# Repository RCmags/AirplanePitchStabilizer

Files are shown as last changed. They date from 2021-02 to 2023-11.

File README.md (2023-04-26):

# Pitch-axis stabilizer for a tail-less airplane :airplane:
This arduino sketch is a servo controller that stabilizes the pitch-axis of a radio-controlled airplane. It's intended to be used on tail-less aircraft to enhance their otherwise marginal stability. Nonetheless, the controller can work on machines with sufficient passive stability. It can increase the effective __static margin__ and allow the center of mass to be shifted aft. This tends to increase the lift-to-drag ratio of the aircraft.  

## State measurement
Pitch stabilization can be accomplished in a variety of ways. These include directly measuring the relative airflow across the aircraft, or measuring changes in the motion and inferring the state of the airflow. 

__Angle of attack sensor__:
The attitude of an airplane is mainly determined by the aerodynamic forces acting upon it. For the pitch axis, the torque generated by these forces is primarily a function of the [angle of attack](https://en.wikipedia.org/wiki/Angle_of_attack). By measuring this angle, one can apply corrective actions that rotate the aircraft towards a particular orientation. Therefore, we can gauge the stability of the aircraft based on how quickly it converges towards said angle, or conversely, its instability if it diverges.    

The simplest angle-of-attack sensor is a [low-friction potentiometer attached to a weathervane](https://www.ilmailu.org/forum/index.php?action=dlattach;topic=5147.0;attach=10336). 

<p align="center"> 
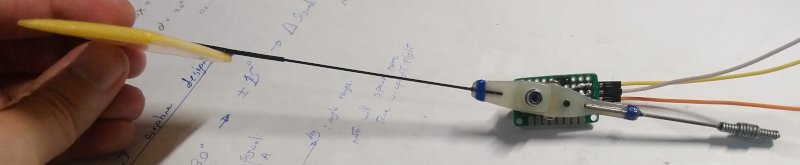
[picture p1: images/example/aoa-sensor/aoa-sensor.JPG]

</p>

As the weathervane will closely follow the local airflow, the deflection of the weathervane is proportional to the angle of attack.

__Inertial measurement unit (IMU)__: 
One can maintain the attitude of the aircraft by measuring its change in orientation and providing an appropriate correction. In this case, we use the angular velocity from a gyroscope as the proportional term in a PID controller. The integral term becomes the angular deflection and is approximately equal to the angle of attack for small external disturbances. As such, we can approximate the behaviour obtained with an angle of attack sensor without having to use a weathervane.  

## Control mechanisms
No matter how the aircraft's state is measured, it is still necessary to use a mechanism to physically rotate the vehicle. The code considers the following designs:

__Trailing edge flaps__: This is the most common way to control a tail-less airplane. It involves deflecting a hinged section of the aft portion of the wing. 

<p align="center"> 
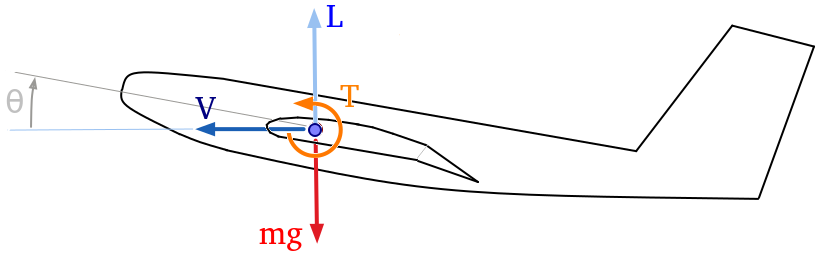
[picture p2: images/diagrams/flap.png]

</p>

The torque generated by these deflections depends on the airspeed and the chord of the wing. If the wing is wider, the flaps are further aft relative to the center of mass and generate a larger torque. Conversely, a higher airspeed causes the changes in lift for a given flap deflection to increase, and this increases the torque. 

Despite their simplicity, trailing edge flaps become _increasingly ineffective_ if the wing has a large [aspect ratio](https://en.wikipedia.org/wiki/Aspect_ratio_(aeronautics)) (small chord) or if the aircraft flies slowly. This configuration is best suited for high speed flight with stubby wings.

__Weight shift__: It is also possible to control the pitch axis by moving the lift vector relative to the center of mass. This comes from the very definition of torque: 

$$ T = d \times F $$

Rather than changing the force __F__ at a known distance __d__ (as with trailing edge flaps), we change the distance in accord to a known force. 

<p align="center"> 
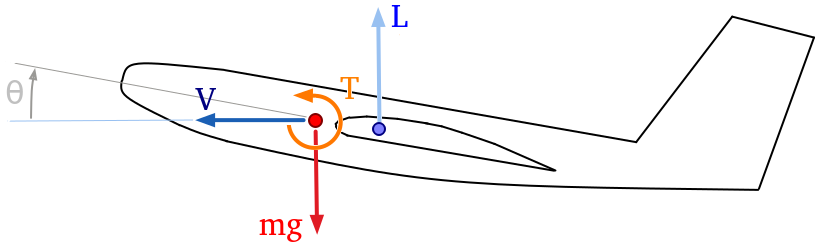
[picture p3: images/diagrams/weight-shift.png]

</p>

In level flight, the net force upon the aircraft is mainly lift, and it must necessarily counter weight. Hence, changing the distance shifts the weight.

$$ F = L = mg $$
 
The effectiveness of this control mechanism is proportional to the magnitude of the lift vector. If the lift is large, small deflections are required. However, the deflections become very large as the lift becomes small. This relationship breaks down with zero lift as there is no force to generate a torque. Despite this flaw, weight shift is a valid control mechanism so long as the airplane's wing remains _loaded_. 

Unlike trailing edge flaps, weight shift does _not_ lose effectiveness at low speed. As long as the aircraft is not accelerating downwards, the control effectiveness will remain the same.  
  
## Schematics
Since there are a few variants of the controller depending on the stabilization method, there are different schematics as well. 

__Nano:__ There are two versions of the sketch for the arduino nano. Despite this, it should be compatible with similar boards. Each version uses the stabilization concepts discussed above. 

- Angle of attack sensor: This schematic assumes a potentiometer is used as the sensor, but any analog sensor will work. A hall sensor is a low-friction alternative of the potentiometer.

<p align="center"> 
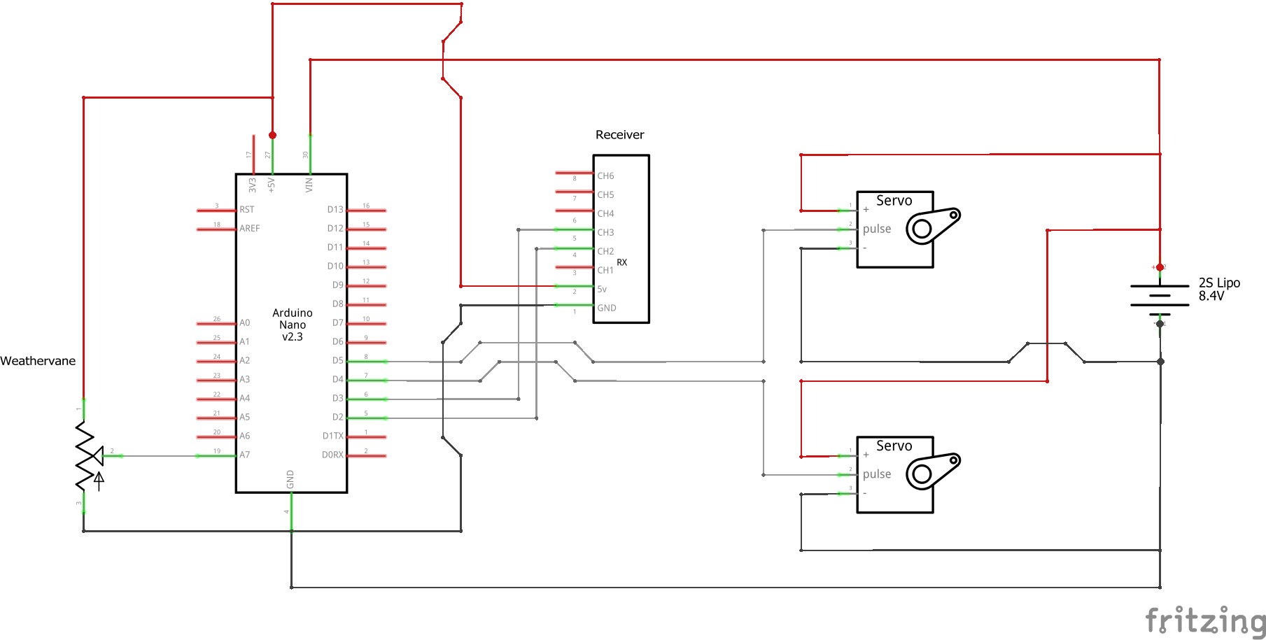
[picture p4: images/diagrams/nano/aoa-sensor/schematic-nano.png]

</p>

- IMU sensor: The code is designed around an [MPU-6050 IMU](https://invensense.tdk.com/products/motion-tracking/6-axis/mpu-6050/) but the general structure will work for any IMU.

<p align="center"> 
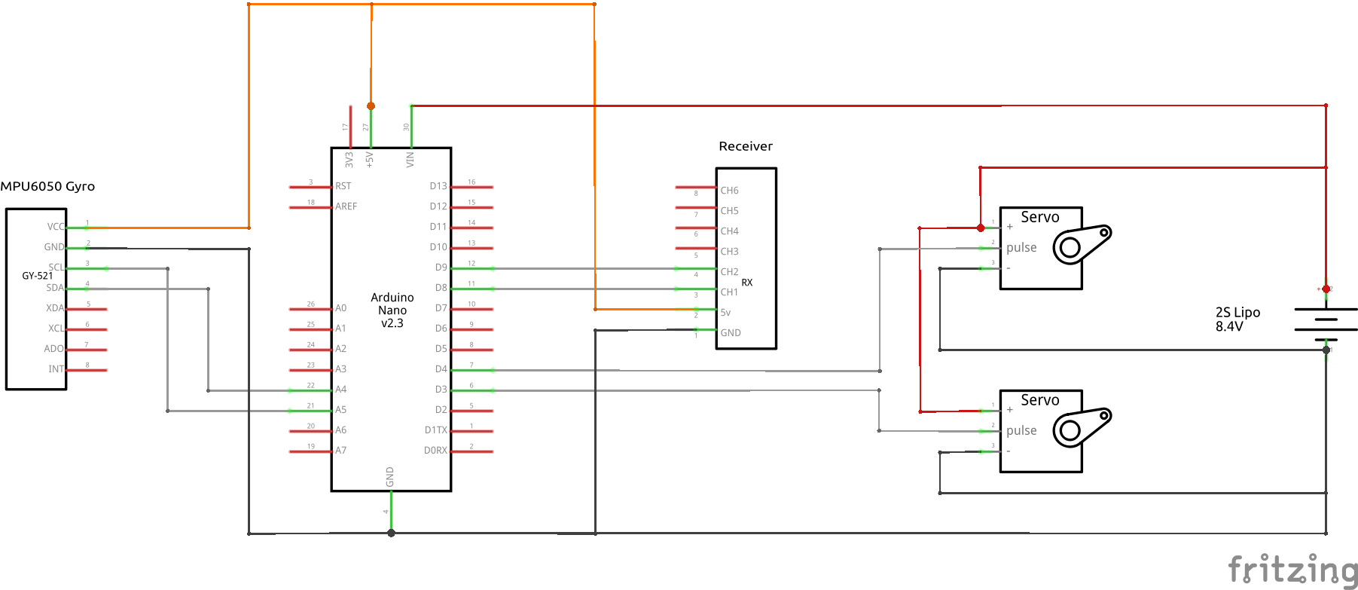
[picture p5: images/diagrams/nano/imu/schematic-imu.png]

</p>

__DigiSpark ATTiny85__: The version of the sketch does not have the option for an IMU. Rather, it serves as a lighter alternative to the nano when using an angle of attack sensor.

<p align="center"> 
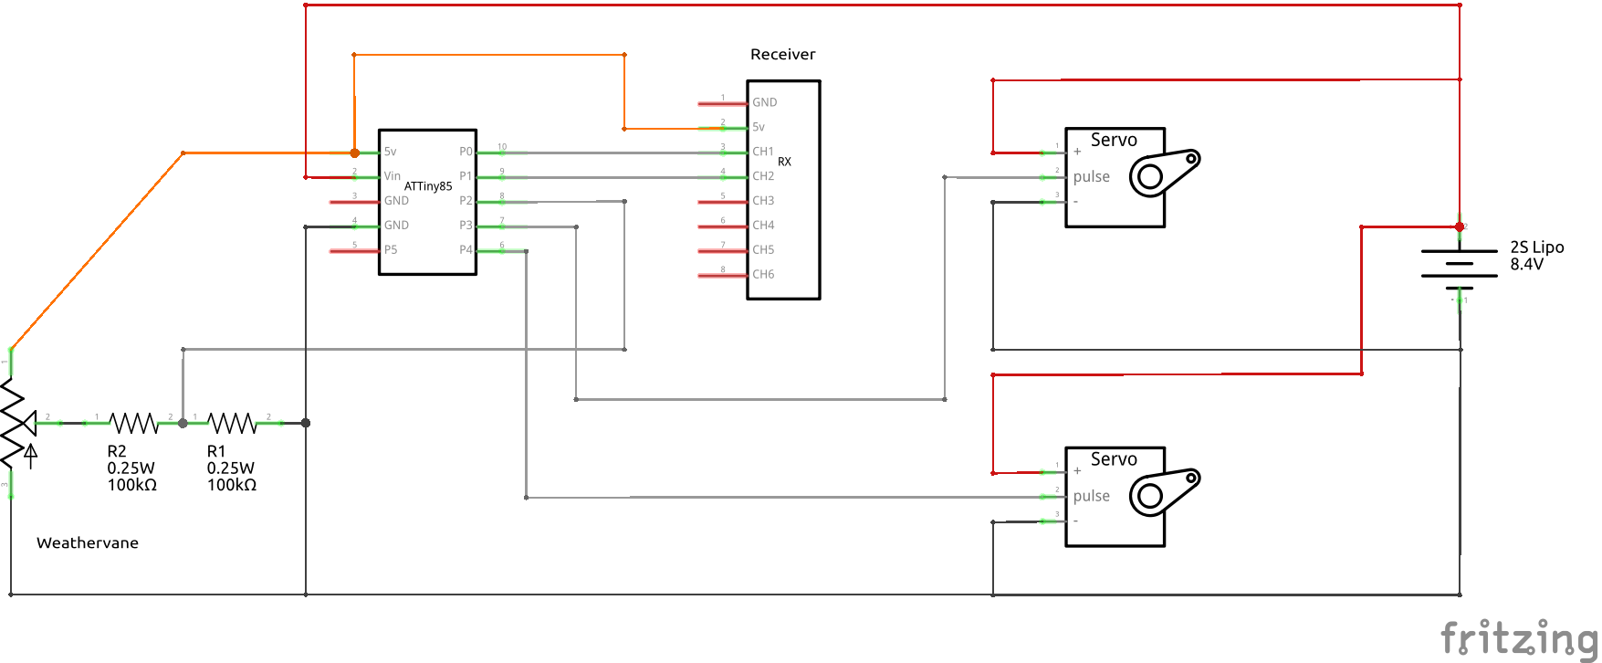
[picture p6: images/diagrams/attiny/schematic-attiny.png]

</p>

## Dependencies
The IMU version of the code requires the following libraries:

- [basicMPU6050](https://github.com/RCmags/basicMPU6050)
- [imuFilter](https://github.com/RCmags/imuFilter)

The ATTiny code requires [ATTinyCore](https://github.com/SpenceKonde/ATTinyCore) to compile. 

## References
See these pages for previous projects that inspired this work:

- [Active flying wing pitch stabilizer concept](http://www.charlesriverrc.org/articles/asfwpp/lelke_activepitch.htm)
- [Unstable Tailless Demonstrator - video](https://www.youtube.com/watch?v=JfKrUbJYk74)

## Examples

- Airplane with a slightly aft center of mass that is controlled by trailing edge flaps: 

<p align="center">
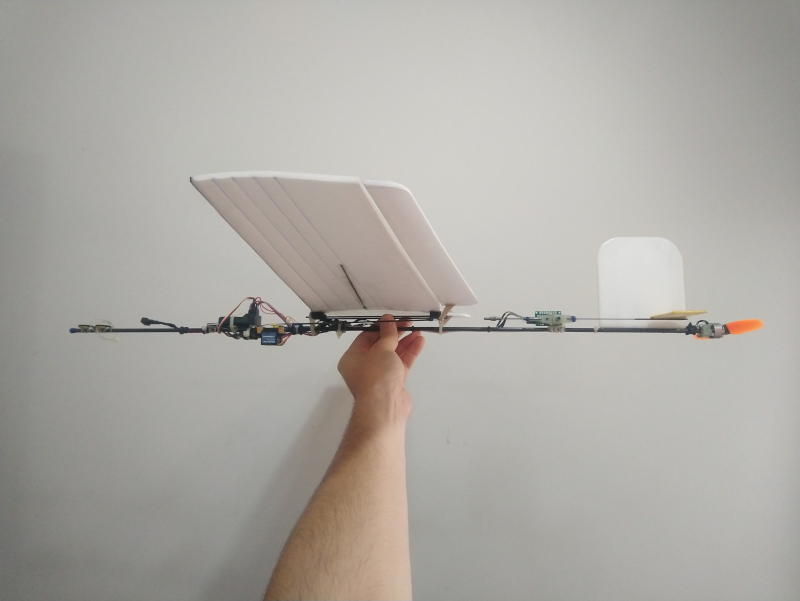
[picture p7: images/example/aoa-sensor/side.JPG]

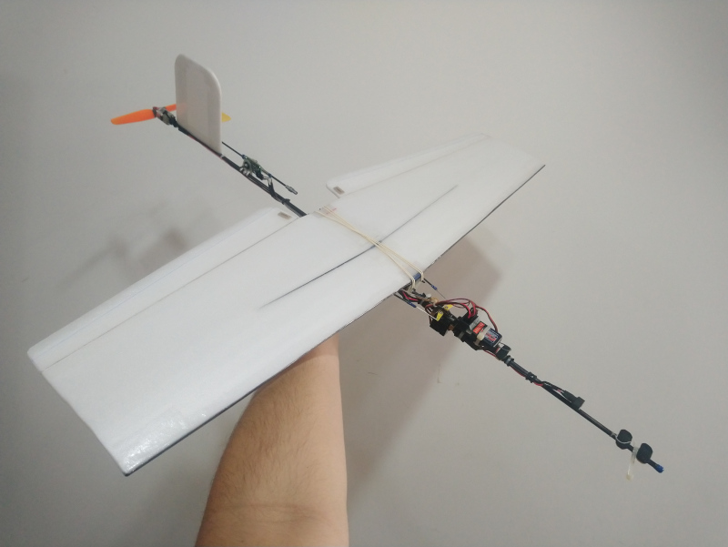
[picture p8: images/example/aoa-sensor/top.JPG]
 
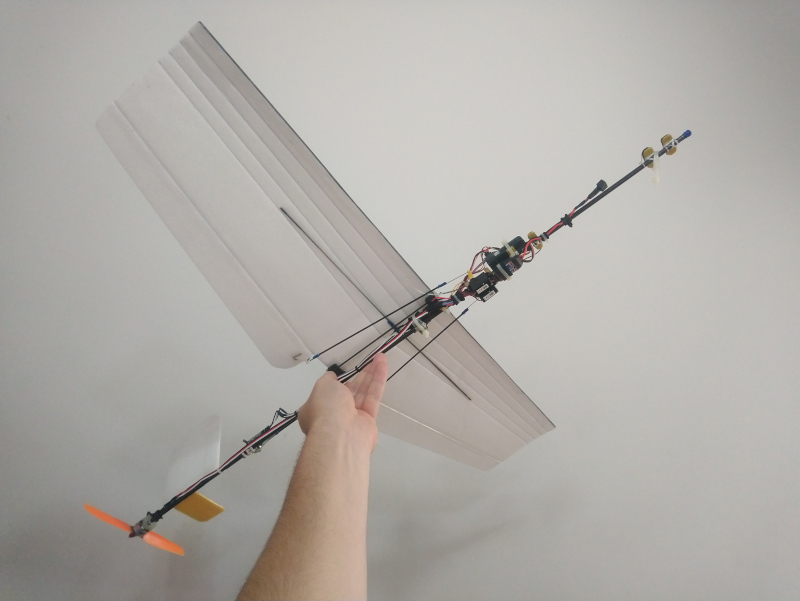
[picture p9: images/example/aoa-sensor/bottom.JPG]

</p>

- Airplane that is stabilized and controlled by weight shift: 

<p align="center">
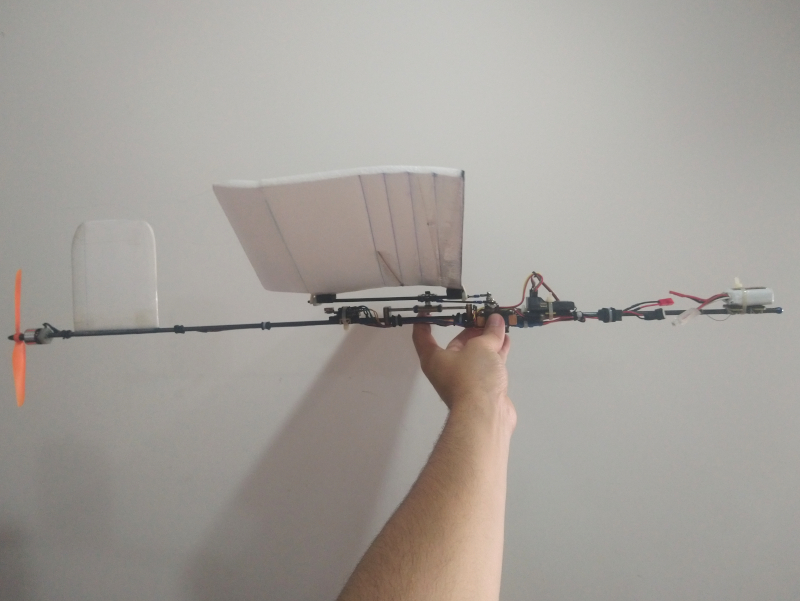
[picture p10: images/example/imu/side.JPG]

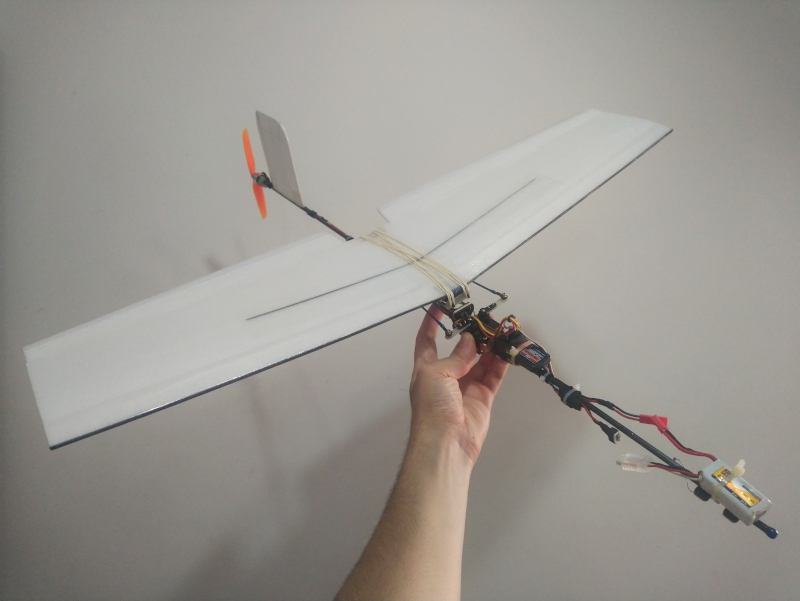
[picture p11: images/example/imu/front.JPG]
 
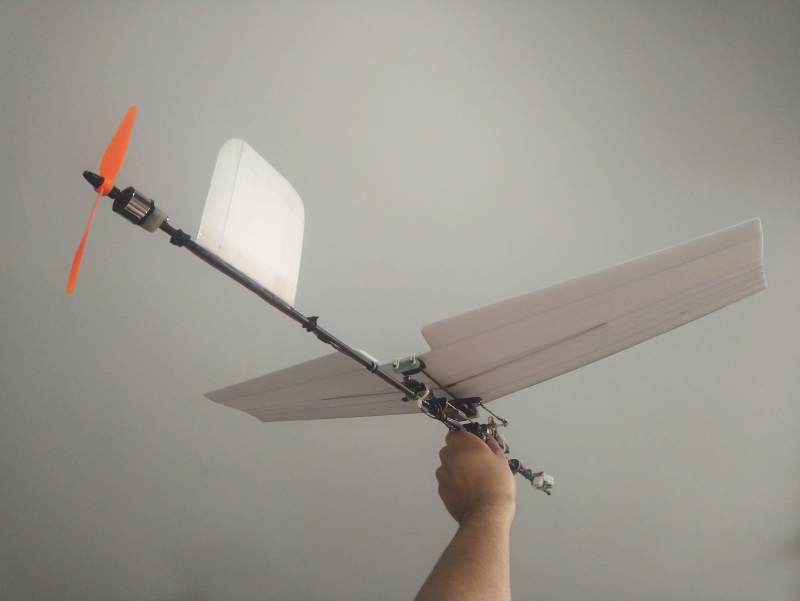
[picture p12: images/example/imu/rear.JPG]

</p>

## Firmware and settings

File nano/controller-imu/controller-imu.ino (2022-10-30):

/* FLYING WING CONTROLLER */

/* Arduino NANO sketch to stabilize an RC flying wing controlled by weight-shift or trailing edge flaps. 
 * It commands two servos and applies V-tail mixing to stabilize the pitch axis.
 * Author: RCmags https://github.com/RCmags
 * 
 * NOTE: 
 * This sketch uses an MPU6050 IMU (gyroscope and accelerometer) to stabilize pitch. It assumes that only 
 * lift and gravity act on the aircraft, and that any external torques are negligible. For stability at 
 * all airspeeds, the wing should have close to no pitching moment.
*/

//=============== Connections ================
// See included schematic
  // Inputs:
// Pin 8  -> Receiver CH1
// Pin 9  -> Receiver CH2
// Pin A5 -> Sensor SCL
// Pin A4 -> Sensor SDA
  // Outputs:
// Pin 2  -> Left  wing servo
// Pin 3  -> Right wing servo 

//=================== Code ===================
#include <Servo.h>
#include "parameters.h"
#include "imu.h"
#include "fusion.h"

//----- constants
constexpr int PWM_MID_L = PWM_MID + TRIM_LEFT;
constexpr int PWM_MID_R = PWM_MID - TRIM_RIGHT;

constexpr float ANGVEL_SCALE = GRAVITY / VELOCITY;   
constexpr float ANGVEL_MIN = (ACCEL_MIN - 1) * ANGVEL_SCALE;
constexpr float ANGVEL_MAX = (ACCEL_MAX - 1) * ANGVEL_SCALE; 

//----- global variables 
Servo servo[2]; 
volatile uint16_t pwm_input[2] = {0};

//----- Input signals
// PORTB = {8 .. 13} -> using pins {8 .. 9} = B00000011

/* port change interrupt to read PWM inputs from receiver */
ISR( PCINT0_vect ) {
  static uint32_t initial_time[2] = {0}; 
  static uint8_t port_last = PINB;  
  
  // port changes
  uint32_t current_time = micros(); 
  uint8_t port_rise = ~port_last & PINB;
  uint8_t port_fall = port_last & ~PINB;
  
  // find changing pins
  for( uint8_t index = 0; index < 2; index += 1) {
    uint8_t mask = B00000001 << index;  // Start at PCINT0
    if( port_rise & mask ) {                
        initial_time[index] = current_time;
    } else if ( port_fall & mask ) {       
        pwm_input[index] = current_time - initial_time[index];
    }
  }
  port_last = PINB;    
}

void setupISR() {
  // enable PORTB interrupts  
  PCICR |= (1 << PCIE0);
  // enable PCINT for pins 8-9     
  PCMSK0 |= (1 << PCINT0);   
  PCMSK0 |= (1 << PCINT1);
  // set as input
  pinMode(8, INPUT_PULLUP);   
  pinMode(9, INPUT_PULLUP); 
}

//----- Input filter

/* average of rx signals */
int* calibrateInputs() {  
  uint32_t sum[2] = {0};
  for( uint8_t count = 0; count < NUMBER_MEAN; count += 1 ) {
    sum[0] += pwm_input[0];
    sum[1] += pwm_input[1];
    delay(20);                  // period of 50hz pwm signal
  }
  static int output[2];         // store value to limit scope
  output[0] = sum[0] / NUMBER_MEAN;
  output[1] = sum[1] / NUMBER_MEAN;
  return output; 
}

/* make variable zero within bounds */
float deadband(float input, const float MIN, const float MAX) {
  return input > MAX ? input - MAX :
         input < MIN ? input - MIN : 0;  
}

/* remove noise from PWM inputs then scale and center */
void filterInputs(float* output) {
  static int* pwm_mean = calibrateInputs();
  static int filter[2] = {0};  
  
  for( uint8_t index = 0; index < 2; index += 1 ) {
    // remove noise
    int input = int( pwm_input[index] );
    int change = input - filter[index]; 
    filter[index] += deadband(change, -INPUT_CHANGE, INPUT_CHANGE);

    // center output
    output[index] = filter[index] - pwm_mean[index];
    output[index] = deadband( output[index], -INPUT_DEADBAND, INPUT_DEADBAND);
  }
  // scale output
  output[0] *= float(GAIN_ROLL);    // roll
  output[1] *= float(GAIN_PITCH);   // pitch
}

//----- PID controller

#ifdef USING_WEIGHT_SHIFT

/* gain to maintain constant torque indifferent of wing load */
float gainLift(float accel) {
  return accel == 0 ? 0 : 1/accel;
}
#endif

/* time integral of variable */
float integral(float input) {
  static uint32_t last_time = micros();
  static float value[2] = {0};

  // update timer
  uint32_t curr_time = micros();
  float dt = float(curr_time - last_time)*1e-6;
  last_time = curr_time;

  // trapezoidal rule
  constexpr float MAX = DEG_TO_RAD * ANGLE_MAX;

  value[0] += 0.5*( input + value[1] )*dt;
  value[1] = input;

  // prevent windup
  value[0] = constrain(value[0], -MAX, MAX);
  return value[0];
}

/* limit wing loading */
float restrictRate(float input, float accel) {  
  // limit target angular velocity
  constexpr float SCALE = (150 * DEG_TO_RAD) / 500.0;     // Convert 500 ms to 150 deg/s
  input *= SCALE;
  input = constrain(input, ANGVEL_MIN, ANGVEL_MAX); 

  // correct rate at acceleration limits
  accel = deadband(accel, ACCEL_MIN, ACCEL_MAX);
  return input - float(GAIN_ACCEL)*accel;
}

/* PID controller to stabilize pitch axis */
float PIDcontroller(float input) {  
  // state 
  float accel = imu.az();       // acceleration due to lift
  #ifdef NEGATE_ACCEL
    accel = -accel;
  #endif

  float angvel_m = imu.gx();    // pitch-axis rotation
  #ifdef NEGATE_GYRO
    angvel_m = -angvel_m;
  #endif
 
  // controller  
  float angvel_t = restrictRate(input, accel);
  float angvel = angvel_m - angvel_t;     
  float angle = integral(angvel);
    // use P and I terms
  float output = float(GAIN_INT)*angle + float(GAIN_PROP)*angvel;

  #ifdef USING_WEIGHT_SHIFT
    return output * gainLift(accel); 
  #else
    return output;
  #endif
}

/* bias controls to self upright */
void autoLevel(float* input) { 
    // horizontal angles
    vec3_t zvec = fusion.getZaxis(LOCAL_FRAME);
    float angle_y = atan2(zvec.x, zvec.z);
    float angle_x = atan2(zvec.y, zvec.z); 
    
    // control rates
    constexpr float ANGLE = ANGLE_TRIM * DEG_TO_RAD;
    input[1] += float(GAIN_ANG_PITCH) * (angle_x - ANGLE);   // pitch
    input[0] += float(GAIN_ANG_ROLL) * angle_y;              // roll
}

//----- Servos
void setupServos() {    
  pinMode(PIN_SERVO_LEFT, OUTPUT);
  pinMode(PIN_SERVO_RIGHT, OUTPUT);
  servo[0].attach(PIN_SERVO_LEFT);
  servo[1].attach(PIN_SERVO_RIGHT);
  // default position
  servo[0].writeMicroseconds(PWM_MID_L);
  servo[1].writeMicroseconds(PWM_MID_R);
}

//----- Main loop

void setup() {
  setupISR();
  setupServos();
  
  #ifndef USING_MANUAL_CONTROL 
    imu.setup();  // use sensor 
    imu.setBias();
    setupFusion();
  #endif
}

void loop() {
  // update gyro calibration 
  imu.updateBias();
  updateFusion();

  // combine inputs
  float input[2]; filterInputs(input);

  #ifndef USING_MANUAL_CONTROL
    #ifdef USING_AUTO_LEVEL
      autoLevel(input);   
    #endif
    input[1] = PIDcontroller( -input[1] );
  #endif
  
  float mix1 = input[0] + input[1];
  float mix2 = input[0] - input[1];
  
  // command servos  
  mix1 = constrain(mix1, -PWM_CHANGE, PWM_CHANGE );
  mix2 = constrain(mix2, -PWM_CHANGE, PWM_CHANGE );

  servo[0].writeMicroseconds( PWM_MID_L + mix1 );    // left wing   
  servo[1].writeMicroseconds( PWM_MID_R + mix2 );    // right wing
}

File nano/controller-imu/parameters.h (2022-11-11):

/*      CONSTANT     |    VALUE   |  UNIT  |   DESCRIPTION */
/*=========================================================*/
//                  1. Control inputs 
//----------------------------------------------------------
#define GAIN_PITCH        1.0                 // Change in target angle of attack due pitch commands. 
#define GAIN_ROLL        -0.9                 // Asymmetric sweep, CH1

//----------------------------------------------------------
//                  2. Servo trims
//----------------------------------------------------------
#define TRIM_LEFT         120      // us       // left  wing 
#define TRIM_RIGHT        0        // us       // right wing

//----------------------------------------------------------
//                  3. Output PWM signal
//----------------------------------------------------------
#define PWM_MID           1500    // us       // Center/middle servo position
#define PWM_CHANGE        750     // us       // Maximum change in servo position

//----------------------------------------------------------
//                  4. Pitch Stabilization
//----------------------------------------------------------
  // I. PID Controller [negate to reverse]                       
#define GAIN_INT          1200.0              // Integral gain. Adjusts spring response
#define GAIN_PROP         1100.0               // Proportional gain. Adjusts damping response
#define ANGLE_MAX         30      // deg      // Angle at which integral term saturates
  
  // II. Self levelling
#define GAIN_ANG_ROLL     200                 // Gain to set roll input to self-level aircraft
#define GAIN_ANG_PITCH   -180                 // Gain to set pitch rate to self-level aircraft 
#define ANGLE_TRIM       -8.0     // deg      // target flight angle relative to horizon
  
  // III. Maximum control rates                          
#define ACCEL_MIN         0.1     // g-force  // Minimum allowable wing load. Seen at max down elevator
#define ACCEL_MAX         3.0     // g-force  // Maximum allowable wing load. Seen at max up elevator
                                              /* NOTE: ACCEL_MIN < ACCEL_MAX */
#define VELOCITY          9.0     // m/s      // Average airspeed. A larger speed reduces the pitch rate 
#define GAIN_ACCEL        0.0                 // Load correction gain. Restricts maximum and minimum accelerations 
                                              /* GAIN_ACC must be positive */

//----------------------------------------------------------
//                  5. Input signal filter
//----------------------------------------------------------
#define INPUT_DEADBAND    24      // us       // deadband near center-stick to prevent integrator drift.
#define INPUT_CHANGE      18      // us       // Change in PWM signal needed to update receiver inputs

//----------------------------------------------------------
//                  6. Settings
//---------------------------------------------------------- 
#define NEGATE_ACCEL                          // Uncomment if sensor reads -1.0g when aircraft is upright (reversed z-axis). 
#define NEGATE_GYRO                           // Uncomment if pitch correction is backwards
#define USING_AUTO_LEVEL                      // Uncomment to enable self-leveling correction
#define USING_WEIGHT_SHIFT                    // Uncomment for weight-shift pitch control.  
                                              /* Enables gain that modifies pitch corrections with angle of attack */
//#define USING_MANUAL_CONTROL                  // Uncomment to dissable pitch stabilization and enable manual input

//----------------------------------------------------------
//                  7. Miscellaneous 
//---------------------------------------------------------- 
#define PIN_SERVO_LEFT    2
#define PIN_SERVO_RIGHT   3
#define NUMBER_MEAN       50                  // number of readings used for input calibration
#define GRAVITY           9.81    // m/^2     // acceleration due to gravity [m/s^2]

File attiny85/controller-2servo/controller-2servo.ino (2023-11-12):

/* FLYING WING CONTROLLER */

/* ATTiny85 sketch to stabilize an RC flying wing controlled by weight-shift or trailing edge flaps. 
 * It commands two servos and applies V-tail mixing to stabilize the pitch axis.
 * Author: RCmags https://github.com/RCmags
 * 
 * NOTE: Code is intended to be used with ATTinyCore
*/

//=============== Connections ================
// See included schematic
  // Inputs:
// Pin 0 -> Receiver CH1
// Pin 1 -> Receiver CH2
// Pin 2 -> middle of voltage divider 
  // Outputs:
// Pin 3 -> Left  wing servo
// Pin 4 -> Right wing servo 

/* VOLTAGE DIVIDER is required for analog input */
/* GND --/\/\/\-- MIDDLE --/\/\/\-- SENSOR_OUT  */
/*        100K              100K                */

//=================== Code ===================
#include <Servo_ATTinyCore.h>
#include "parameters.cpp"

//----- constants
constexpr int PWM_MID_L = PWM_MID + TRIM_LEFT;
constexpr int PWM_MID_R = PWM_MID - TRIM_RIGHT*GAIN_CORRECTION;

//---- global variables 
Servo servo[2]; 
volatile uint16_t pwm_input[2] = {0};

//----- Input signals
// PORTB = {0 .. 5} -> using pins {0 .. 1} = B00000011

/* port change interrupt to read PWM inputs from receiver */
ISR( PCINT0_vect ) {
  static uint32_t initial_time[2] = {0}; 
  static uint8_t port_last = PINB;  
  
  // port changes
  uint32_t current_time = micros(); 
  uint8_t port_rise = ~port_last & PINB;
  uint8_t port_fall = port_last & ~PINB;
  
  // find changing pins
  for( uint8_t index = 0; index < 2; index += 1) {
    uint8_t mask = B00000001 << index;  // Start at PCINT0
    if( port_rise & mask ) {                
        initial_time[index] = current_time;
    } else if ( port_fall & mask ) {       
        pwm_input[index] = current_time - initial_time[index];
    }
  }
  port_last = PINB;    
}

void setupISR() {
  // enable pin change interrupts
  GIMSK |= (1 << PCIE);     
  // set pins as PCINT
  PCMSK |= (1 << PCINT0);   
  PCMSK |= (1 << PCINT1);
  // set as input
  pinMode(PB0, INPUT_PULLUP);   
  pinMode(PB1, INPUT_PULLUP); ; 
}

//----- Input filter

/* remove noise from PWM inputs then scale and center */
void filterInputs(float* output) {
  static int filter[2] = {0};  
  
  // apply deadband filter
  for( uint8_t index = 0; index < 2; index += 1 ) {
    int change = int( pwm_input[index] ) - filter[index]; 
    filter[index] = change >  INPUT_CHANGE ? int(pwm_input[index]) - INPUT_CHANGE :
                    change < -INPUT_CHANGE ? int(pwm_input[index]) + INPUT_CHANGE : filter[index];
  }
  // scale and center inputs
  output[0] = float( filter[0] - PWM_MID )*GAIN_ROLL;    // roll
  output[1] = float( filter[1] - PWM_MID )*GAIN_PITCH;   // pitch
}

//----- Analog sensor

/* read sensor and calibrate to degrees */
float readSensor() {
  constexpr float SLOPE = float(ANGLE_MAX - ANGLE_MIN) / float(ANALOG_MAX - ANALOG_MIN);
  constexpr int   CONST = (ANALOG_MAX + ANALOG_MIN)/2 + ANALOG_OFFSET;
  // scale reading
  int value = analogRead(1) - CONST;      // PB2 -> ADC1 
  return SLOPE*float(value);
}

/* remove noise from analog sensor and calculate derivative */
void filterSensor(float *xbar, float *dxdt) {
  // store state
  static uint32_t last_time = micros();
  static float x[2] = {0}, v = 0;

  // time change
  uint32_t curr_time = micros();
  float dt  = float(curr_time - last_time)*1e-6;
  last_time = curr_time; 

  // alpha-beta filter:
  constexpr float BETA = ALPHA * ALPHA * 0.25;
    // error
  float xi = readSensor();
  float dx = 0.5*( xi - x[1] );
    // position
  float xnew = x[0];
  xnew += v*dt;  
  xnew += ALPHA * dx; 
    // velocity
  v += BETA * dx/dt;

  // store past position
  x[1] = x[0];
  x[0] = xnew;

  // return smoothed value and derivative
  *xbar = xnew;
  *dxdt = v;
}

//----- PID controller

#ifdef USING_WEIGHT_SHIFT

/* gain to maintain constant torque indifferent of angle of attack */
float gainAngle(float angle) {
  return angle == 0 ? 0 : AOA_TRIM/angle;
}
#endif

/* PID controller to stabilize pitch axis */
float PIDcontroller(float input) {
  float angle; float angle_deriv; filterSensor(&angle, &angle_deriv);
  
  // desired angle of attack
  constexpr float SCALE = 10.0 / 500.0;     // Convert 500 ms to 10 degrees
  
  float targ_angle = SCALE*input + AOA_TRIM;
  targ_angle = constrain(targ_angle, AOA_MIN, AOA_MAX);
  
  // use P and D terms
  float output = GAIN_PROP*(angle - targ_angle) + GAIN_DERIV*angle_deriv;
  
  #ifdef USING_WEIGHT_SHIFT
    return output * gainAngle(angle); 
  #else
    return output;
  #endif
}

//----- Servos

void setupServos() {    
  pinMode(PB3, OUTPUT);
  pinMode(PB4, OUTPUT);
  servo[0].attach(PB3);
  servo[1].attach(PB4);
  // default position
  servo[0].writeMicroseconds(PWM_MID_L);
  servo[1].writeMicroseconds(PWM_MID_R);
}

//----- Main loop

void setup() {
  setupISR();
  setupServos();
  pinMode(PB2, INPUT_PULLUP); // sensor
}

void loop() {
  // combine inputs
  float input[2]; filterInputs(input);

  #ifdef USING_MANUAL_CONTROL
    float output = input[1];                    // directly use rx input
  #else
    float output = PIDcontroller( -input[1] );  // pitch input controls target AoA
  #endif

  // limit
  output = constrain(output, -PWM_CHANGE_PITCH, PWM_CHANGE_PITCH); 

  // mix
  float mix1 = input[0] + output; 
  float mix2 = input[0] - output;
  
  // command servo  
  mix1 = constrain(mix1, -PWM_CHANGE, PWM_CHANGE);
  mix2 = constrain(mix2, -PWM_CHANGE, PWM_CHANGE) * GAIN_CORRECTION;

  servo[0].writeMicroseconds( PWM_MID_L + mix1 );    // left wing
  servo[1].writeMicroseconds( PWM_MID_R + mix2 );    // right wing 
}

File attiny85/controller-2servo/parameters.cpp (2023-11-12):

/*      CONSTANT     |    VALUE   |  UNIT  |   DESCRIPTION */
/*=========================================================*/
//                  1. Control inputs
//----------------------------------------------------------
#define GAIN_PITCH       -1.0               // Change in target angle of attack due pitch commands 
#define GAIN_ROLL         0.65               // Asymmetric sweep/ailerons

//----------------------------------------------------------
//                  2. Servo trims
//----------------------------------------------------------
#define TRIM_LEFT         0       // us     // left  wing 
#define TRIM_RIGHT        0       // us     // right wing
                                            /* Adjust so the aircraft maintains altitude without rolling or pitching */

//----------------------------------------------------------
//                  3. Output PWM signal
//----------------------------------------------------------
#define PWM_MID           1500    // us     // Center/middle servo position
#define PWM_CHANGE        800     // us     // Maximum change in servo position relative to middle
#define PWM_CHANGE_PITCH  800     // us     // Maximum change in servo position for pitch 
#define GAIN_CORRECTION   0.6               // Correction factor to make servos move symmetrically

//----------------------------------------------------------
//                  4. Signal filters
//----------------------------------------------------------
#define INPUT_CHANGE      12      // us     // Change in PWM signal needed to update receiver inputs
#define ALPHA             0.15              /* Gain of alpha-beta filter applied to sensor input. 
                                               A smaller value smoothens the reading at the cost of slower response */
//----------------------------------------------------------
//                  5. Pitch Stabilization
//----------------------------------------------------------
  // I. PID Controller [negate to reverse] 
#define GAIN_PROP         90.0              // Proportional gain. Adjusts spring response
#define GAIN_DERIV        1.0               // Derivative gain. Adjusts damping response. Must have same sign as GAIN_PROP
  
  // II. Input restrictions
#define AOA_TRIM          1.5     // deg    // Target angle of attack in level flight 
#define AOA_MIN          -15.0    // deg    // Minimum target angle of attack. Prevents wings unloading
#define AOA_MAX           15.0    // deg    // Maximum taget angle of attack. Prevents stall
                                            /* NOTE: AOA_MIN < AOA_TRIM < AOA_MAX */

//----------------------------------------------------------
//                  6. Sensor calibrationg
//----------------------------------------------------------
#define ANGLE_MAX         15      // deg    // Largest deflection of angle sensor 
#define ANGLE_MIN        -15      // deg    // Smallest deflection of angle sensor
                                            /* NOTE: ANGLE_MIN < ANGLE_MAX */
#define ANALOG_MAX        370               // AnalogRead output at largest deflection
#define ANALOG_MIN        95                // AnalogRead output at smallest deflection
#define ANALOG_OFFSET     0                // Offset to make the sensor read zero at the wing's zero-lift angle of attack

//----------------------------------------------------------
//                  7. Settings
//----------------------------------------------------------
//#define USING_WEIGHT_SHIFT                  // Uncomment for weight-shift pitch control.  
                                            /* Enables gain that modifies pitch corrections with angle of attack */ 
//#define USING_MANUAL_CONTROL                // Uncomment to dissable pitch stabilization and enable manual input

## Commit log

2022-09-29 imu stab
2022-10-19 flight tested imu
2022-10-24 input filter
2023-04-25 moved images, add diagrams
    [tailless-attiny.fzz, tailless-imu.fzz, tailless-nano.fzz]
2023-11-12 fix calibrate
    [tailless-attiny.fzz, tailless-imu.fzz]
